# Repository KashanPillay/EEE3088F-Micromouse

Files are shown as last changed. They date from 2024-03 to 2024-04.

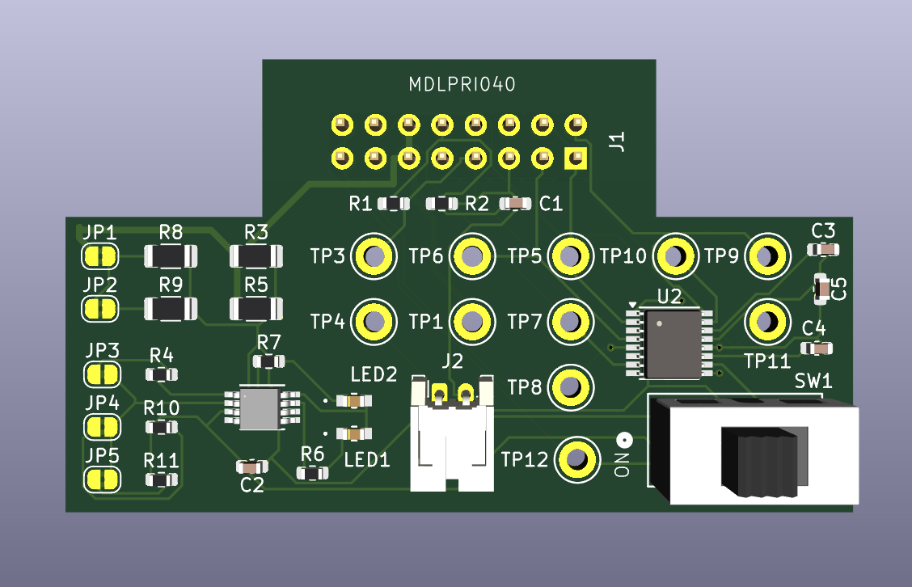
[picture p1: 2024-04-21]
Power Subsystem/Interim Report Figures/3D.png

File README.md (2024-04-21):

# EEE3088F-Micromouse
A repository to manage and control versions pertaining to the EEE3088F Micro-mouse Project and all sub-projects.
This GitHub contains 2 folders, each carrying relevant information regarding a specific subsystem: the first is Sensing and the second is Power. There are multiple folders within each subsystem folder. There is one containing all the datasheets for components selected for the final designs. These folders are labeled "Data sheets". In addition, there is a folder titled 'Interim Design Report' in each subsystem which contains the completed Interim Design Report. Lastly, all Gerber files and Bill Of Materials files can be found in the last folder. Thank you for visiting the GitHub :)

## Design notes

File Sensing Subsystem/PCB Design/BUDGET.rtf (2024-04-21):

BUDGET:

Sensor: SFH309 - $0.325/unit - $0.975
Emitter: TSAL6200 - $0.089/unit - $0.534

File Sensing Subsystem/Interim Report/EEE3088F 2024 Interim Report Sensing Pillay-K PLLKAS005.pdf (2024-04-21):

# Interim Design Report

Micromouse: Sensing Subsystem


Prepared by:
Kashan Pillay
PLLKAS005

Prepared for:
EEE3088F
Department of Electrical Engineering University of Cape Town

April 21, 2024

# Declaration

1. I know that plagiarism is wrong. Plagiarism is to use another’s work and pretend that it is one’s own.
2. I have used the IEEE convention for citation and referencing. Each contribution to, and quotation in, this report from the work(s) of other people has been attributed, and has been cited and referenced.
3. This report is my own work.
4. I have not allowed, and will not allow, anyone to copy my work with the intention of passing it off as their own work or part thereof.

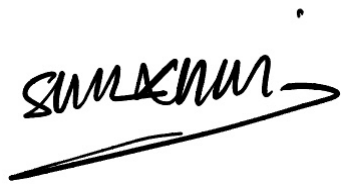
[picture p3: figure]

April 21, 2024

Kashan Pillay | Date

ii

# Contents

1 Introduction | 1
2 Requirements Analysis | 2
3 Subsystem Design | 5
4 Acceptance Testing | 10

iii

# Chapter 1

# Introduction

### 1.1 Problem Description

This project is a task in which a sensing subsystem is to be designed and manufactured for fitment in a fully functioning micro-mouse.
The greater project is a micro-mouse. A micro-mouse is in essence, a maze-solving robot. The focus of this project is on the hardware backing the robot. There are four aspects of the hardware to be taken into account when designing the specific subsystem solution - in this case the sensing subsystem -; the processor, the motherboard, sensing and power. The motherboard will be responsible for connecting all four PCBs and is the base that all other modules will connect to. The processor board - which makes use of an STM32L476 - will be the control module of the robot which will involve a small software aspect in order to see its functioning correctly. The power module powers all aspects of the robot and lastly, the sensing subsystem - around which this project report will be based - is responsible for the detection of the surroundings of the robot.
In keeping with the goal of the project, this specific subsystem (sensing) is to detect the presence of an obstacle (in the most likely case, a maze wall) in front of and to either side of the functioning micro-mouse. In addition, this subsystem should have the means to save power when not in operation while abiding by all the set-out requirements and specifications within the scope of work.

### 1.2 Scope and Limitations

The scope of this project is to design and manufacture a sensing subsystem that will provide information to the processor on whether there is an obstruction in the way of the micro-mouse. The processor and motherboard will be provided and the group partner is designing the power subsystem. Of the objectives of this subsystem, detection sits are the forefront. Detection needs to be in front of and on either side of the robot. In addition, the following objectives are also to be implemented:
- Designing for reliability.
- Taking into account power draw in order to ensure that the micro-mouse is able to solve the maze without the battery being drained completely.
- A small software aspect in order to properly integrate this subsystem with the micro-controller and visibly indicate its functionality.
There are several limitations that need to be considered:
- Design Limitation: The subsystem PCB should be a suitable size for the robot and compatible with the motherboard pin headers.
- Time Limitation: The final complete and working PCB is to be demonstrated on 13/05/2024.
- Cost Limitation: There is a cost restriction of $16.50 for both boards ($8.25 per board).

### 1.3 GitHub Link

Group 62 GitHub link. (https://github.com/KashanPillay/EEE3088F-Micromouse)

# Chapter 2

# Requirements Analysis

### 2.1 Requirements

The requirements for a micro-mouse sensing module are described in Table 2.1 below.

Requirement ID | Description
UR01 | The design must maneuver within the confines of the maze.
FR01 | The design PCB should be an appropriate size.
FR02 | The design PCB must cost within the specified budget.
UR03 | The design must detect obstacles
FR03 | The design must be able to indicate location/detection ability.
UR04 | The design must provide real-time input to the micro-controller.
FR04 | The design PCB must be compatible with the motherboard.
UR05 | The design must be powered externally.
FR05 | The design must adhere to power and current restrictions.
UR06 | The design must have a power-saving functionality.
FR06 | The design input supply must be pulse width modulated.
UR07 | The design components must all be sourced from the manufacturer.
FR07 | The design must be manufactured by a specific company and all components must be specified.

Table 2.1: User[UR] and Functional[FR] requirements of the sensing subsystem design.

### 2.2 Specifications

The specifications, refined from the requirements in Table 2.1, for the micro-mouse sensing module are described in Table 2.2.

Specification ID | Description
SP01 | The PCB design must not exceed the bounds of an 85mm² square.
SP02 | The design must not exceed $8.25 per board ($16.50 total).
SP03 | The design must use a different LED to indicate detection - in the front, left or right - of the three available LEDs.
SP04 | The design PCB must be compatible with a 2x14 (2.4mm pin pitch) pin header.
SP05-1 | The design must be powered by 3.5V to 3.7V.
SP05-2 | The design must have a current draw of no more than 400mA.
SP06 | The pulse width modulation must be set to 50%.
SP07 | The manufacturing must be with JLCPCB and all components must be specified on the production files with a stock of more than 1000.

Table 2.2: Specifications[SP] of the sensing subsystem derived from the requirements in Table 2.1.

### 2.3 Testing Procedures

A summary of the acceptance testing [AT] procedures detailed in chapter 4 is given below in Table 2.3. Reference Key:
’AT’ - Acceptance Testing; ’UT’ - Unit Testing; ’UAT’ - User Acceptance Testing; ’BAT’ - Business

2.4. Traceability Analysis

Acceptance Testing.

AT ID | AT Type | Description
AT01 | UAT | Measure the manufactured PCB or ensure the dimensions of the PCB enclosed in the production files are adequate.
AT02 | BAT | Review the manufacturing order cost.
AT03-1 | UT | Observe a different LED turn on for detection in front of and on either side of the robot and no LED turning on when no detection.
AT03-2 | UT | Measuring the voltage across the emitters of the sensing circuit.
AT03-3 | UT | Measuring the output voltage of the sensing circuit.
AT04 | UT | Using a calliper to measure pin header through-hole connections.
AT05-1 | UT | Measuring the input voltage of the sensing circuit.
AT05-2 | UT | Measuring the input current of the sensing circuit.
AT06 | UT | Ensuring the micro-controller has been set to provide an output signal that has a duty cycle of 50%.
AT07 | BAT | Review the manufacturing bill of materials.

Table 2.3: Acceptance Testing [AT] descriptions derived from the table of requirements in Table 2.1.

### 2.4 Traceability Analysis

The show how the requirements, specifications and testing procedures all link, Table 2.4 is provided.

| Requirements | Specifications | Acceptance Test
1 | UR01,FR01 | SP01 | AT01
2 | FR02 | SP02 | AT02
3 | UR03, FR03 | SP03 | AT03-1, AT03-2, AT03-3
4 | UR04, FR04 | SP04 | AT04
5 | UR05, FR05 | SP05-1, SP05-2 | AT05-1, AT05-2
6 | UR06, FR06 | SP06 | AT06
7 | UR07, FR07 | SP07 | AT07

Table 2.4: Requirements Traceability Matrix

### 2.4.1 Traceability Analysis 1

UR01 and so FR01 - the appropriate size requirement in order to allow for the robot to have adequate mobility within the maze is from which SP01, the specification that dictates the size of the PCB should be no greater than the bounds of an 85mm x 85mm square, can be derived. In order to ’test’ that this requirement is satisfied - AT01 is suggested, which is to measure the manufactured PCB or ensure the dimensions on the production files are sufficient.

### 2.4.2 Traceability Analysis 2

From FR02, requiring the cost of the PCB manufacturing to be within a certain budget, SP02 -dictating that the design should not cost more than $8.25 per board ($16.50 total) - can be derived. These can be verified through AT02 which entails reviewing the manufacturing order cost to ensure that it is below the specified limit.

2.4. Traceability Analysis

### 2.4.3 Traceability Analysis 3

UR03 and so FR03 - the aspect that requires the system to detect obstacles and indicate its location gives rise to the specification SP03 which is that the design must use a different LED to indicate detection in the front, left and right of the robot. To test for this, we can use AT03-1, AT03-2 and AT03-3. AT03-1 indicates that to test for successful application of requirements, we should observe a different LED turn on for detection at each location and no LED being on when there is no detection. AT03-2 suggests measuring the voltage across the emitters in order to ensure that they are functioning as required and AT03-3 suggests measuring the voltage output of each of the three sensing circuits to observe that a high output is at the circuit of the location in which there is an obstacle.

### 2.4.4 Traceability Analysis 4

UR04 and FR04 - is the requirement that indicates that the design must provide a real time input to the micro-controller (UR04) and to do this the design PCB must be compatible with the motherboard pin headers (FR04) leads to SP04 which specifies that the design PCB must be compatible with a 2x14 (2.4mm pin pitch) pin header. In order to validate this requirement, AT04 suggests using a calliper to measure the pin header through hole connections present in the design.

### 2.4.5 Traceability Analysis 5

UR05 and FR05 - the requirements that dictate the power of the system should be external which requires observing power and current restrictions brings forth the specification which says that the design should be powered by 3.5V to 3.7V (SP05-1) while having a current draw of no more than 400mA (SP05-2). In order to validate this AT05-1 suggests measuring the input voltage of the sensing circuit to observe its adherence to the specification SP05-1 and AT05-2 suggests measuring the input current to observe its adherence to the specification SP05-2.

### 2.4.6 Traceability Analysis 6

UR06 indicates that the design input supply must have a power-saving functionality and that is accomplished by FR06 which entails having an input supply from a PWM port. This gives rise to specification SP06 which indicates that the pulse width modulation must be set to 50% and AT06 suggests a way to validate this is to observe the micro-controller port output has been set to the desired duty cycle.

### 2.4.7 Traceability Analysis 7

UR07 - the requirement that indicates that all components should be sourced from the PCB manufacturer can be accomplished by FR07 which states that the design must be manufactured by a specific company and all required components must be comprised within the BOM that will sent to them. From the above, we can see how SP07 came about which specifies that all manufacturing must be with JLCPCB with components being in stock in excess of 1000 units. AT07 suggests a way in which we can validate this which is to review the manufacturing bill of materials (BOM) in order to confirm that all required components were requested.

# Chapter 3

# Subsystem Design

### 3.1 Design Decisions

In this section, two of the most crucial aspects of the design process are going to be explored - Circuit Component Selection and PCB Design Selection. From these two aspects, various design decisions are going to be made.

### 3.1.1 Circuit Component Selection

- Infrared Sensor:
Three different infrared sensors were considered when designing this sensing subsystem the QRD1114, (https://www.onsemi.com/pdf/datasheet/qrd1114-d.pdf) SFH309FA (https://look.ams-osram.com/m/ce14b97f1982f0f/original/SFH-309-FA.pdf) and SFH205. (https://look.ams-osram.com/m/74e24481854c49f8/original/SFH-205-FA.pdf)
| QRD1114 | SFH309FA | SFH205
Pro | -Detection at up to 200mm. -Both an IR emitter and IR receiver. | -Sensitivity: 730-1120nm. -Size: 0.45mmx0.45mm. -Quantity in stock: 1632 -Cost: $0.2696 | -Sensitivity: 800-1100nm. -Size: 2.65mmx2.65mm. -Cost: $0.5940
Con | -Quantity in stock: 5. -Cost: $1.57 -Part Type: Extended | -Simply an IR receiver. -Part Type: Extended | -Quantity in stock: 0 - Simply an IR receiver. - Part Type: Extended

Table 3.1: Pros and Cons of the considered infrared sensors.

Selected Infrared Sensor Design Decision:
SFH309FA - based on the spectral sensitivity, small component size, large in stock quantity and low cost. This sensor is able to provide all the sensing abilities of the other two, with the added stock and cost benefits.
Discarded Infrared Sensor Design Decision:
QRD1114 - based on the low in stock quantity and high cost, this option was not feasible. SFH205 -due to the part not being in stock, it was immediately removed from consideration.
- Infrared Emitter:
Three different infrared emitters were considered when designing this sensing subsystem the QRD1114, (https://www.onsemi.com/pdf/datasheet/qrd1114-d.pdf) TSAL6100 (https://www.vishay.com/docs/81009/tsal6100.pdf) and TSAL6200. (https://www.vishay.com/docs/81010/tsal6200.pdf)
| TSAL6200 | TSAL6100 | QRD1114
Pro | -Peak emission: 940nm -Cost: $0.1194 -Quantity in Stock: 1476 | Peak emission: 940nm -Cost: $0.1205 -Half intensity angle: 10 deg | -Peak emission: 940nm. -Both an IR emitter and IR receiver.
Con | -Part Type: Extended -Half intensity angle: 17 deg | -Quantity in stock: 0 -Part Type: Extended | -Quantity in stock: 5. -Cost: $1.57 -Part Type: Extended

Table 3.2: Pros and Cons of the considered infrared emitters.

Selected Infrared Emitter Design Decision:
TSAL6200 - based off of the peak emission, large in stock quantity and low cost. This sensor is able to provide all the emitting abilities of the other two, with the added stock and cost benefits.
Discarded Infrared Emitter Design Decision:

3.1. Design Decisions

QRD1114 - based on the low in stock quantity and high cost, this option was not feasible. TSAL6100
- due to the part not being in stock, it was immediately removed from consideration - however was initially considered due to low cost and good angle of half intensity.
- Emitter Circuit Transistor:
Two bipolar junction transistors were considered for use as a switch in the emitter circuit of this sensing subsystem, the MMBT3904 and MMBT3904-G.
| MMBT3904 | MMBT3904-G
Pro | -Cost: $0.0097 -Quantity in stock: 1096136 -Part Type: Basic | -Cost: $0.0063 -Quantity in stock: 369248
Con | -Ic(max) is 200mA. -Power Dissipation: 200mW | -Part Type: Extended -Power Dissipation: 225mW

Table 3.3: Pros and Cons of the considered bipolar junction transistors.

Selected BJT Design Decision:
MMBT3904 - based off of the lower power dissipation, high in stock quantity and basic part classification. Discarded BJT Design Decision:
MMBT3904-G - based off of the greater power dissipation and extended part classification.
- E24 Component Values:
The use of E24 values was considered for the capacitors and resistors in this subsystem, however, since most resistors and capacitors are available in E12 values, basic components were easy to source in large quantities and low cost. In discarding the idea of E24 values, certain E12 values were selected to ensure that calculated component values were the same, if not extremely close. Some of the benefits of using the E24 series are the wider range of values as well as lesser associated tolerance.

### 3.1.2 PCB Design Selection

- Component Quantities/Configurations:
| Dual Emitter/Sensor Compo-nent | Single Sensor and Emitter | Single Sensor and Dual Emitter
Pro | -Single component allowing for PCB modularity. | -Cost: $0.38 per pair, so $1.167 per board. -Emission: sufficient IR light emission to be detected after re-flection. | -Cost: $0.50 per set, so $1.52 per board. -Emission: excellent IR light emission to be detected after re-flection.
Con | -Cost: $1.57 per unit, so $4.71 per board to allow for all direc-tion detection. -Emission: Combination compo-nent has a poor emittance and so additional emitters will be re-quired. | -Coverage: Detection of IR light from source in addition to re-flected light. -Reflection Loss:A single emitter results in a portion of IR light lost due to the angle at which the emitter and sensor are placed. | -Coverage: Detection of IR light from the source in addition to reflected light.

Table 3.4: Pros and Cons of the considered component quantities and configurations.

Selected Component Quantity Design Decision:
The single sensor and dual emitter design was selected due to the enhanced infrared emittance to ensure better detection for the required locations and distances. While the single sensor and emitter

3.1. Design Decisions

design was acceptable, the single sensor and dual emitter was within the confines of the budget and enhanced.
Discarded Component Quantity Design Decision:
The dual component design was discarded due to the cost implications and poor performance - relative to the other two designs. The single sensor and emitter was discarded for the enhanced ability of the dual emitter option.
- PCB Shape and Size:
| Square | Rectangle | T-shape
Pro | -Does not jut out of the robot allowing for good mobility. | -The large PCB coverage allows for sufficient room for all neces-sary circuitry. | -Sufficient room for all the nec-essary circuitry without protrud-ing from the robot allowing for range of motion.
Con | -Inadequate visibility (created by extension) to allow for com-plete obstacle detection on the left and right of the robot. | -Protruding from the robot, dis-abling a complete range of mo-tion within the confines of the maze. | -Minimal protruding which will reduce the motion of the robot in the maze.

Table 3.5: Pros and Cons of the considered PCB shape and size.

Selected PCB Shape and Size Design Decision: The chosen shape and size design decision is the T-shape. This is as a result of the minimal protruding, while still extending enough to allow for the IR sensor to adequately detect obstacles from a distance point of view as well allowing visibility
- in that the sensors visibility will not be hindered by parts of the robot.
Discarded PCB Shape and Size Design Decision: The square and rectangle designs were discarded. The square - due to the dimensions allowing for the sensors visibility to be hindered by parts of the robot and the rectangle due to its size disabling a wide range of motion for the robot within the walls of the maze (200x200mm).

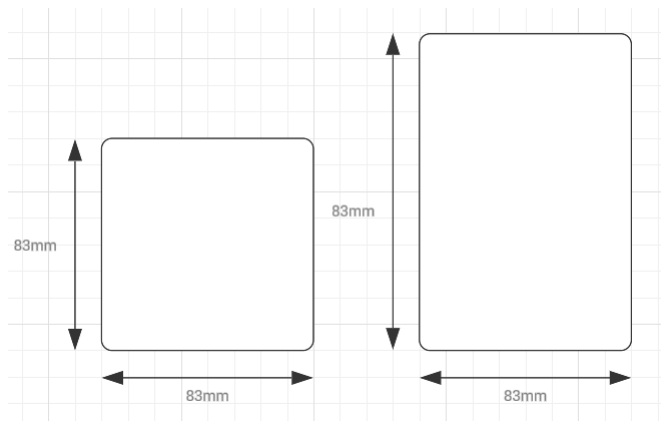
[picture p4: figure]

Figure 3.1: Square/Rect Shape

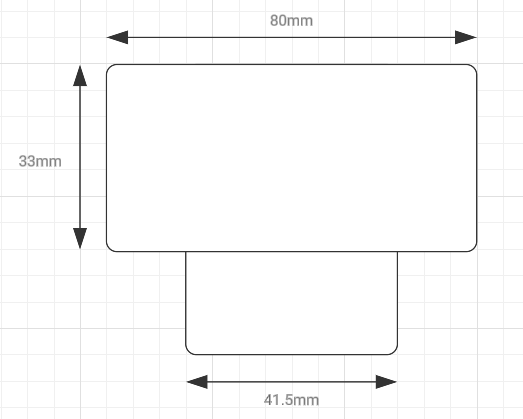
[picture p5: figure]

Figure 3.2: T Shape

- Sensor Placement and Angle:
Selected Sensor Placement and Angle Design Decision:
The chosen angle and placement was at 90 degrees with a wall to the left and right of the robot. This is in order to ensure maximum reflected IR light returning and not having to take into consideration IR reflected light lost due to the angle and distance at which the sensor is in relation to an obstacle on either side of the robot.
Discarded Sensor Placement and Angle Design Decision:
The 45 degree angle placement was discarded due to the poor detection ability of the sensors due to the distance at which the obstacle would be should the sensor be angled in this manner.

3.1. Design Decisions
| 45 degrees | 90 degrees
Pro | -Allows for better placed cir-cuitry on the manufactured PCB. | -Maximum detection ability due to proximity to reflective surface and orthogonal nature of reflec-tion.
Con | -Poor detection ability due to distance from the reflected sur-face/obstacle. | -PCB needs to be protruding in order to circumvent the sensors being obstructed by parts of the robot.

Table 3.6: Pros and Cons of the considered sensor placement and angle.

### 3.1.3 Final Design

The following design was selected based off of the above six unique design decisions. A sensing module is going to consist of a single SFH309FA infrared sensor accompanied by two TSAL6200 infrared emitters on either side. This is going to allow for adequate infrared light to be reflected and so detected by the SFH309FA. There are going to be three of these sensing modules that comprise the full sensing subsystem, one facing forward, one facing ninety degrees to the left and one facing ninety degrees to the right. So as to ensure the obstacle is within sensing range. These are all going to be mounted on a T-shaped PCB which allows for an adequate range of motion for the robot without compromising the visibility of the sensing module.

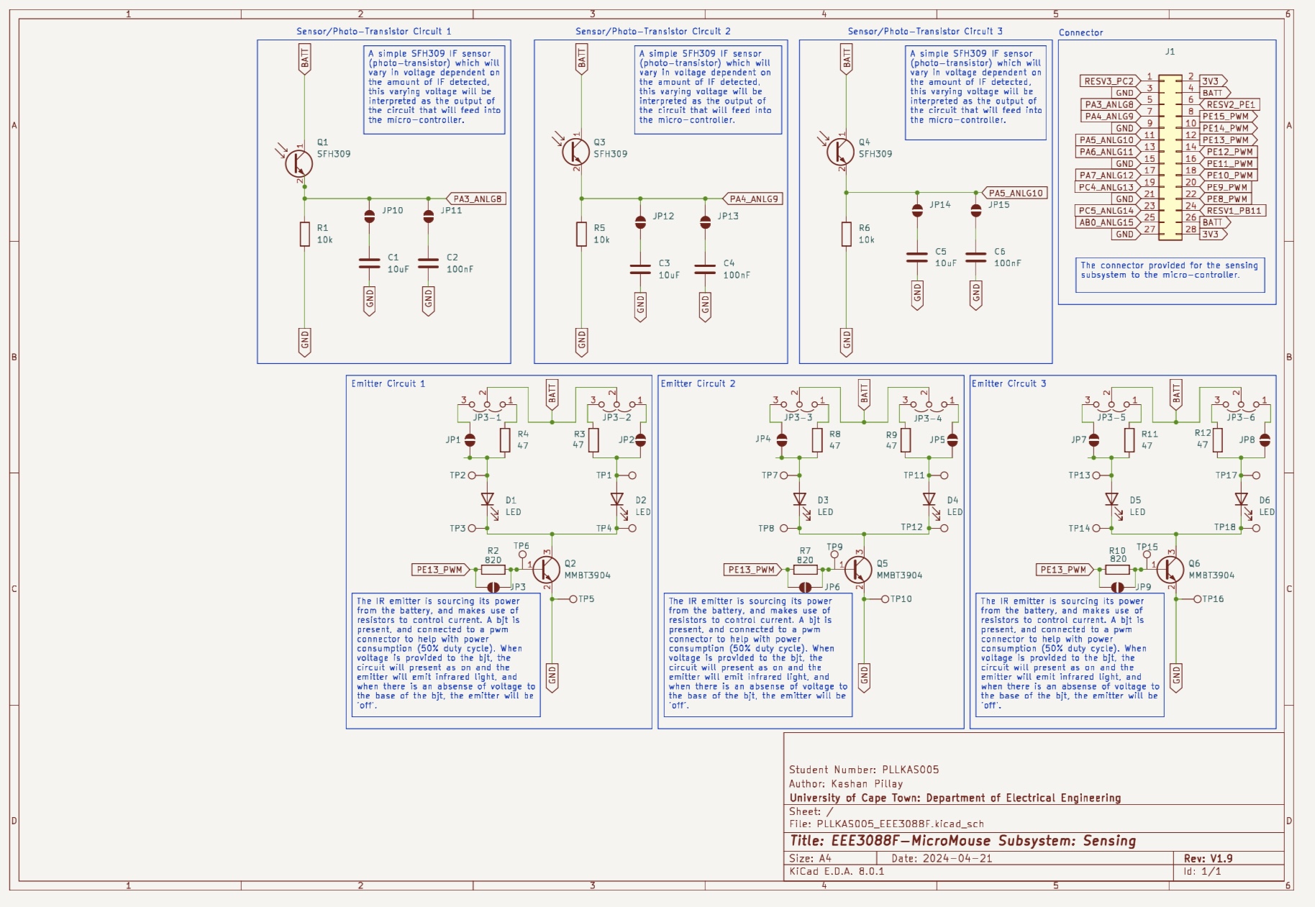
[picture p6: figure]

Figure 3.3: Final Design Schematic

CALCULATIONS: (Emitter Circuit 1)
Source Voltage = 3.3V, Current Draw = 0.1A, Forward Voltage = 1.2V ( TSAL6200) (https://www.vishay.com/docs/81010/tsal6200.pdf) R4=(3.3V-1.2V)/0.05A=42Ohms. E12: R4 = 47Ohms. Similarly R3=R8=R9=R11=R12= 47Ohms

PWM Voltage = 3.3V, Vce = 0.7V and Ib = 3.33mA (for Ic = 100mA) ( MMBT3904) (https://www.diodes.com/assets/Datasheets/MMBT3904.pdf) KVL:3v3-Vce=I(R2). R2=(3.3V-0.7V)/0.0033A=787Ohms. E12: R2=820Ohms. Similarly R7=R10=820Ohms.

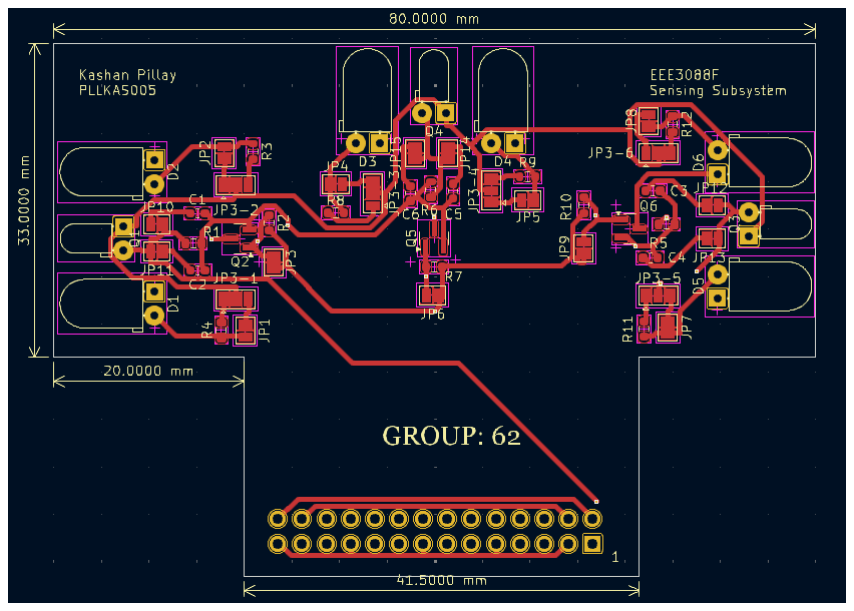
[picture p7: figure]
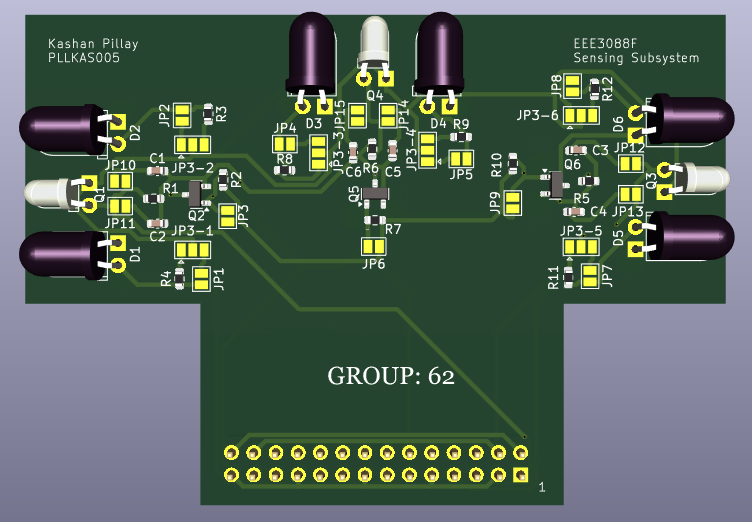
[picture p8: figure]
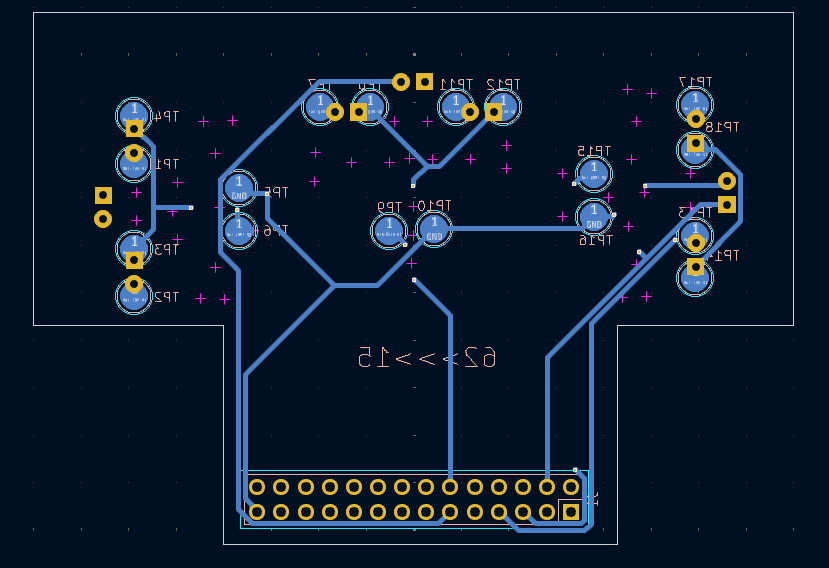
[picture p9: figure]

(a) Front PCB | (b) Back PCB | (c) 3D PCB

Figure 3.4: PCB

3.2. Failure Management

### 3.2 Failure Management

Below, Table 3.7 summarises the precautions taken to account for design errors/flaws.

Measure | Description
3-Point Jumpers (open) | i. These jumpers have been used at the voltage input of both branches of each emitter circuit. This jumper allows for the use of solder to connect the input voltage to a branch of choice in order to resolve a calculation error for the resistor at this point.
Test Points | i. These have been used to provide the voltage drop across the infrared emitter in order to ascertain the functional status of this component. ii. These have been used to provide the voltage drop across the base-emitter junction of the bipolar junction transistor (emitter circuit) in order to ensure that the transistor is operating in the desired (linear) region.
Pad-Jumper (open) | i. These have been used in the additional branch of the input voltage to each emitter circuit. This allows the addition of a different valued resistor or to completely short the branch. ii. These have been used across the resistor in the base of the bjt in order to all for the decrease of resistance by the addition of a resistor in parallel. iii. These have been used as connectors to two different capacitors at the output of each infrared sensor circuit in order to allow for selection between the two different valued components.
Additional Ca-pacitors | i. These are connected to the circuit using open solder pad jumpers in order to allow for error catching in the integration with the ADC.

Table 3.7: Failure Management Measures

### 3.3 System Integration and Interfacing

Below, Table 3.8 and Figure 3.5 summarise the integral integration and interfacing aspects.

Interface | Description | Pins/Output
I001 | Sensing-subsystem to Processor-subsystem (housing the STM32L476) in order for the micro-controller (ADC) to receive the output of the sensor circuit (obstacle detection) of the sensing subsystem. | • ANLG8: PIN5 to STM PA3 • ANLG9: PIN7 to STM PA4 • ANLG10: PIN11 to STM PA5
I002 | Processor-subsystem (housing the STM32L476) to Sensing-subsystem in order for there to be power from the source to the emitter circuit of the sensing subsystem. | • STM BATT to PIN26
I003 | Sensing-subsystem to Processor-subsystem (housing the STM32L476) in order to have ground as a reference. | • PIN21 to STM GND
I004 | Processor-subsystem (housing the STM32L476) to the Sensing-subsystem in order to reduce power consumption a PWM signal is supplied to the base of the emitter circuit, control the bjt which is acting as a switch. | • PWM: STM PE13 to PIN12

Table 3.8: System Interfacing Table

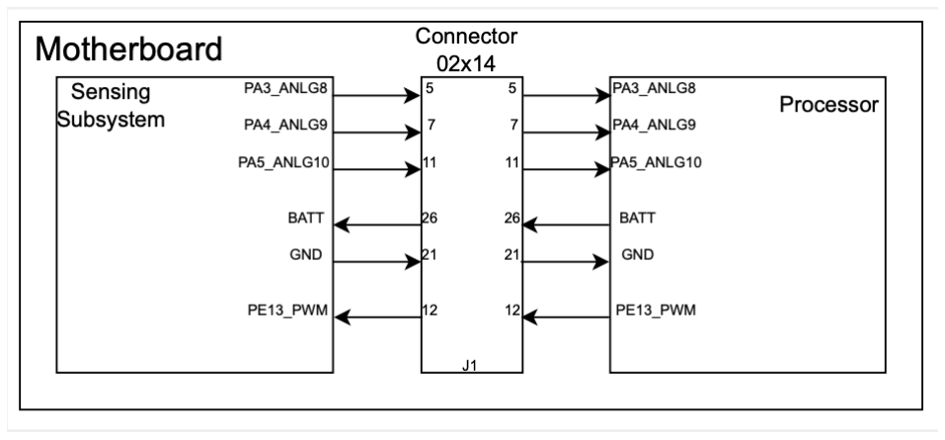
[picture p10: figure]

Figure 3.5: System Interfacing Diagram

# Chapter 4

# Acceptance Testing

### 4.1 Tests

AT ID | Description | Testing Procedure | Pass Criteria
AT01 | (User Acceptance Testing) Measure the man-ufactured PCB or ensure the dimensions of the PCB enclosed in the production files are adequate. | i. Measure the length of the manufactured PCB with a PCB ruler. ii. Measure the breadth of the manu-factured PCB with a PCB ruler. | i. Dimension of length less than 85mm. ii. Dimension of breadth less than 85mm.
AT02 | (Business Acceptance Testing) Review the manufacturing order cost. | i. By looking at the confirmation of receipt or order receipt the cost can be confirmed. | i. The total cost being less than $16.50.
AT03-1 | (Unit Testing) Observe a different LED turn on for detection in the front of and on either side of the robot and no LED turning on when no detection. | i. Place an obstacle in front of the powered micro-mouse ii. Place an obstacle to the left of the micro-mouse. iii. Place an obsta-cle to the right of the micro-mouse. iiii. Have no obstacles in the surroundings of the robot. | i. LED one lights up. ii. LED two lights up. iii. LED three lights up. iiii. None of the three LEDs turn on.
AT03-2 | (Unit Testing) Measuring the voltage across the emitters of the sensing circuit. | i. Using a voltmeter, measure the voltage across the emitters us-ing the placed testing points. | i. Voltage in the range of 1.2-1.6V.
AT03-3 | (Unit Testing) Measuring the output voltage of the sensing circuit. | i.Using a voltmeter, measure the output voltage across the placed test points. | i. The voltage being in the range of 0.5-3.3V. (there should be an out-put voltage - due to ambient light)
AT04 | (Unit Testing) Measuring the pin header through-hole connections. | i. Using a caliper, mea-sure the through-hole connections. | i. The measurement being in the range of 2.4mm.

4.1. Tests
AT ID | Description | Testing Procedure | Pass Criteria
AT05-1 | (Unit Testing) Measuring the input voltage of the sensing circuit. | i.Using a voltmeter, measure the input volt-age with respect to ground. | i. The input voltage should be in the range of 3.3V.
AT05-2 | (Unit Testing) Measuring the input current of the sensing circuit. | i.Using an ammeter, measure the input cur-rent of the circuit. | i. The current should be less than 100mA.
AT06 | (Unit Testing) Ensuring the micro-controller has been set to provide an output signal that has a duty cycle of 50%. | i. Using the suggested interface software, en-code the required duty cycle. | i.The duty cycle should be less than 100% to ensure any sort of power saving.
AT07 | (Business Acceptance Testing) Review the manufacturing bill of materials. | i.By looking at the con-firmation of receipt or order receipt the com-ponent selection can be confirmed. | i. Components should be populated on PCB and the order con-firmed.

Table 4.1: Subsystem Acceptance Tests

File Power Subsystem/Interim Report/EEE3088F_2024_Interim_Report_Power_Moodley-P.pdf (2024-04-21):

# Interim Design Report

Micromouse Power Subsystem


Prepared by:
Priya Moodley
MDLPRI040

Prepared for:
EEE3088F
Department of Electrical Engineering University of Cape Town

April 21, 2024

# Declaration

1. I know that plagiarism is wrong. Plagiarism is to use another’s work and pretend that it is one’s own.
2. I have used the IEEE convention for citation and referencing. Each contribution to, and quotation in, this report from the work(s) of other people has been attributed, and has been cited and referenced.
3. This report is my own work.
4. I have not allowed, and will not allow, anyone to copy my work with the intention of passing it off as their own work or part thereof.

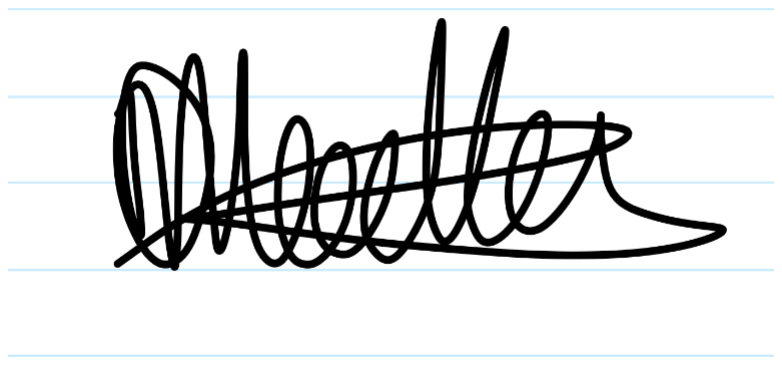
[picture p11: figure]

April 21, 2024

Name Surname | Date

# Contents

1 Introduction | 1
2 Requirements Analysis | 2
3 Subsystem Design | 5
4 Acceptance Testing | 10

# Chapter 1

# Introduction

### 1.1 Problem Description

The project’s problem is to design and manufacture a power subsystem that is capable of powering an entire micro-mouse system.

The greater project comprises four subsystems that interface with one another, each of which has a related board. The motherboard carries two motors and is the foundation for the other boards: the processor board, sensor board, and power board (upon which the power subsystem will be implemented). The processor board contains the microcontroller and its related input/output pins which allow for operations to be dictated as required. The sensor subsystem can determine whether there is an obstruction in front and on either side of the robot and output that to the user as well as change its direction according to its findings. The power subsystem is responsible for powering each of the above-mentioned boards which, if they behave as intended, allow the robot to solve a maze correctly.

### 1.2 Scope and Limitations

The power subsystem will provide power to the two motors, the STM32L476 microcontroller on the processor board, and the sensors contained within the sensing subsystem. This ensures that all subsystems receive the required power to function as intended, and should it not behave correctly, the micro-mouse operation will be affected. Additionally, the power board will be fully equipped with a charging circuit to charge the battery. Without a functional charging circuit, the power provided to the above-mentioned subsystems will be limited to a single battery life. The power board containing the power subsystem will be an appropriate size as the micro-mouse in itself will be physically small and a large power board will affect the micro-mouse’s center of mass and restrict the motion of the mouse in a maze.

There will be an ON/OFF switch with specific current limitations. Furthermore, there are specific connectors that must be catered for to allow for interfacing with the other subsystems. There is a financial limitation placed on the subsystem as the component cost budget for a single board is $ 8.25, which includes the fee for extended components. In addition, the time limitation states that the design must be completed by 24 March 2024 to allow for the manufacturing process to begin and the completed power board must be prepared for presentation on 8 May 2024.

### 1.3 GitHub Link

Click here to visit Group 62’s GitHub (https://github.com/KashanPillay/EEE3088F-Micromouse)

# Chapter 2

# Requirements Analysis

### 2.1 Requirements

The requirements for a micromouse power module are described in Table 2.1.

Table 2.1: User and functional requirements of the power subsystem.

Requirement ID | Description
UR01 | Provide power to the motors.
FR01 | A motor driver circuit is used to provide the appropriate voltages to the motors.
UR02 | Provide power to the microcontroller.
FR02 | Have a connection from the microcontroller’s battery pin to the battery.
UR03 | Design must only include components from a PCB manufacturing company.
FR03 | All components must be found on JCLPCB.
UR04 | Fit onto the motherboard.
FR04 | Must have a tab with the connectors on the power board.
UR05 | Must be able to move within a maze.
FR05 | Ensure the board’s length does not interfere with the micromouse’s center of rotation.
UR06 | Adhere to a strict budget.
FR06 | Select components whose sum does not exceed the budget.
UR07 | Design must be able to be switched ON and OFF.
FR07 | Have a physical ON/OFF switch that controls voltage to the other components.
UR08 | Monitor the battery’s state of charge.
FR08 | Provide an analog connection with the voltage of the battery to the microcontroller.
UR09 | Charge the battery.
FR09 | Have a battery charging circuit that accounts for when the external voltage source is plugged in and when it is removed.

### 2.2 Specifications

The specifications, refined from the requirements in Table 2.1, for the micromouse power module, are described in Table 2.2.

Table 2.2: Specifications of the power subsystem derived from the requirements in Table 2.1.

Specification ID | Description
SP01 | Motors have a maximum current draw of 200mA at 4.2V from the battery.
SP02 | 2x8 JST (2.54mm pin pitch) Pin Header joins the battery and microcontroller pins.
SP03 | There must be a stock of over 500 on JCLPCB for each component.
SP04 | The centered tab has a minimum height of 18mm and a maximum width of 35mm.
SP05 | The board length must not exceed 100mm.
SP06 | The components must cost under $ 8.25 per board, including extended part fees.
SP07 | Use a switch to turn the power board ON/OFF and ensure it is labeled on the board.
SP08 | Monitors and sends the battery’s state of charge to the BATT-ADC pin.
SP09 | Attach the battery to the power board using a two-pin 2mm JST pin header.
SP10 | The max discharge must be at 0.5C for the 3.7V 800mAh Lithium-Polymer battery.

2.3. Testing Procedures

### 2.3 Testing Procedures

A summary of the testing procedures detailed in chapter 4 is given in Table 2.3.

Table 2.3: A brief review of the testing procedures

Acceptance Test ID | Description
AT01 | Check that motors receive power.
AT02 | Check that the microcontroller is receiving power.
AT03 | Check that all components are within acceptable stock limits on the JLCPCB website.
AT04 | Measure the width and length of the tab.
AT05 | Measure the width and length of the entire power board.
AT06 | Calculate the total component cost and verify it on the JLCPCB website.
AT07 | Check that the switch behaves correctly.
AT08 | Code the microcontroller to display the state of charge from the ADC pin.
AT09 | Check that the battery charging circuit is operational.

### 2.4 Traceability Analysis

The show how the requirements, specifications, and testing procedures all link, Table 2.4 is provided.

Table 2.4: Requirements Traceability Matrix

# | Requirements | Specifications | Acceptance Test

1 | UR01, FR01 | SP01 | AT01
2 | UR02, FR02 | SP02 | AT02
3 | UR03, FR03 | SP03 | AT03
4 | UR04, FR04 | SPO4 | AT04
5 | UR05, FR05 | SP05 | AT05
6 | UR06, FR06 | SP06 | AT06
7 | UR07, FR07 | SP07 | AT07
8 | UR08, FR08 | SP08 | AT08
9 | UR09, FR09 | SP09, SP10 | AT09

### 2.4.1 Traceability Analysis 1

UR01 states that the motors must receive power from the power subsystem. In FR01 it is explained that a motor driver circuit must be used to do so, and SP01 states the maximum current through the output of that circuit. To test this AT01 is suggested because it verifies that power is being sent to the motors and that they are within the accepted current limits.

### 2.4.2 Traceability Analysis 2

From UR02, which says that the microcontroller is powered by the power subsystem, and FR02 which expands that a connection is required, SP02 can be derived because a specific pin header is needed to correctly interface with the other subsystems. AT02 ensures that the power is being correctly provided to the microcontroller.

2.4. Traceability Analysis

### 2.4.3 Traceability Analysis 3

From UR03 and FR03, which state the requirement that all components must come from the same PCB manufacturing company- JLCPCB - SP03 can be derived as there needs to be adequate availability for a component to be populated on a board. These can be tested through AT03 which checks the quantity in stock for each component on the JLCPCB website.

### 2.4.4 Traceability Analysis 4

As seen in UR04 and FR03, the power board must have a tab with the specific dimensions titled in SP04 to ensure that it fits onto the motherboard comfortably. AT04 checks that these conditions are satisfied by measuring the dimensions and comparing them against the required values.

### 2.4.5 Traceability Analysis 5

UR05 and FR05 are concerned with the size of the power board as it will affect the movement of the micromouse as a whole, SP05 is a specification derived from the overall measurements of the micromouse and ensures that the power board does not extend too far past the end of the micromouse. This is tested through AT05 which measures the length of the power board.

### 2.4.6 Traceability Analysis 6

From UR06 and FR06, there is a strict financial requirement where the component cost cannot exceed $ 8.25 per board as specified in SP06, and AT06 verifies that the financial requirements are adhered.

### 2.4.7 Traceability Analysis 7

UR07 and FR07 state the need for a physical ON/OFF switch and SP07 details the necessary condition for a label on the board to ensure there is proper communication from the board to those using it. AT07 uses a continuity test on a multimeter to ensure that it is working as intended.

### 2.4.8 Traceability Analysis 8

UR08 and FR08 ensure that the battery’s state of charge is monitored and sent to a specific pin in the microcontroller, specified in SP08 and verified by AT08 which uses the microcontroller to display the output of the BATT-ADC pin.

### 2.4.9 Traceability Analysis 9

The battery charging circuit, explained by UR09 AND FR09 with specifications from SP09 and SP10 outlines the need for a functional battery charging circuit that is effective when the battery is plugged into a voltage source and once it is removed. The output of the circuit is tested by AT09.

# Chapter 3

# Subsystem Design

### 3.1 Design Decisions

### 3.1.1 Component Selection

Motor Driver Circuit

For the motor driver circuit, multiple options were considered. An H-Bridge configuration is the most common solution as it allows for bidirectional control of the motor and speed control from Pulse-Width Modulation (PWM) signals from the microcontroller. Some H-Bridges can be constructed from scratch with MOSFETs or switches, and there are Integrated Circuits (ICs) that contain those components as internal circuitry. Ultimately, as the budget permitted it, an IC was chosen. This was a more promising route as there was less room for error than if the circuit was designed from scratch. In addition, a Dual H-Bridge IC will contain the functionality for both motors in a single component which saves space on the board and expenses if a suitable one is picked.

JLCPCB contains a multitude of Dual H-Bridge Motor Driver ICs, however, parts were filtered based on the following criteria:
- There must be stock
- The part cannot be unavailable
- There must be an English data sheet or an English version available online
- The supply voltage or PWM signal voltage must be in the range provided (3.7V and 3.3V, respectively)
- The IC must be able to handle a maximum of 400mA on the motor side
- It must be a dual H-Bridge Motor, therefore able to operate two DC motors as a single device • The IC must only require inputs from I/O Pins that are available to the power board

The first 3 viable options that fit all criteria are shown below in Figure 3.1:

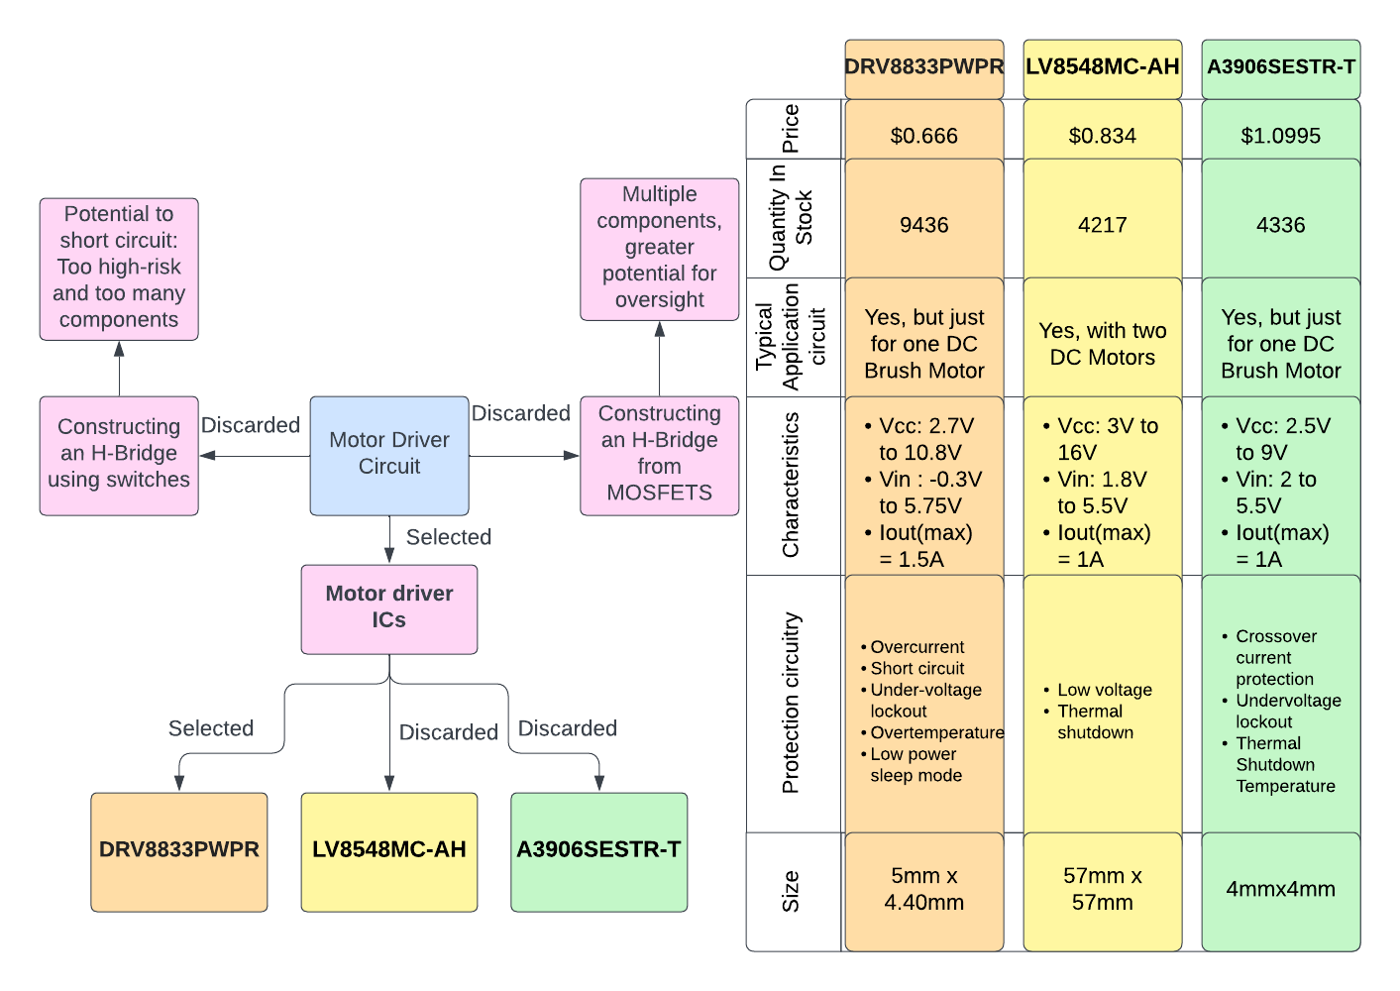
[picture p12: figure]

Figure 3.1: Flow Chart with Motor Circuit options and Table comparing Motor Driver ICs

3.1. Design Decisions

As seen in the figure above, the DRV8833PWPR is the cheapest option, has more protection circuitry, and is physically small so as not to take up too much space on the power board, it fulfills all the voltage and current requirements. Thus, the DRV8833PWPR whose data sheet can be found here (https://wmsc.lcsc.com/wmsc/upload/file/pdf/v2/lcsc/1810151712_Texas-Instruments-DRV8833PWPR_C50506.pdf) was the final choice for the Motor Driver IC.

Battery Charging Circuit

For the battery to be charged, the appropriate circuit must be constructed. After a search on JLCPCB, it was found that there are three basic Battery Charging ICs that have the same functionality as building a battery charging circuit. The English data sheet for the TP4057 could not be found, so the selection was between the TP4054 and the TP4056. Both components are preset to 4.2V Charge Voltage and are adaptable to charging Single Cell Li-Ion Batteries directly from the USB Port. These are very similar components but their differences are recorded in the table below:

Table 3.1: Table comparing two Battery Charging ICs

| TP4054 | TP4056
Price | $0.1289 | $0.1724
Quantity in Stock | 9468 | 107298
BAT Pin Current(max) | 800mA | 1200mA

Ultimately, the choice was made as the TP4056 contained an informative table on exactly which resistors to pick for specific desired battery currents while the TP4054 has many varying equations which resulted in various contradictory answers for the resistance. The price difference (among others) is minimal between the two ICs. The data sheet for the TP4056 can be found here. (https://dlnmh9ip6v2uc.cloudfront.net/datasheets/Prototyping/TP4056.pdf)

Switch

There are only extended part switches that were considered for this project. A slide switch was considered the most appropriate as it has a definitive state of ’ON’ and ’OFF’. After filtering out those that were not in stock, four hundred and twenty-five options were remaining.

Since the switch functionality is fairly simple, the first compatible switch on the list with the right specifications was selected. That was the SS-12D10G5 slide switch. The cost is $0.2618 and the average cost for slide switches varies from around $0.1 to $0.4 so this was an acceptable figure and there are 2362 in stock. Additionally, it is an adequate size to allow for easy switching but not too bulky for the final power board. The data sheet can be found here. (https://wmsc.lcsc.com/wmsc/upload/file/pdf/v2/lcsc/2110100830_XKB-Connectivity-SS-12D10G5_C2884744.pdf)

### 3.1.2 Calculations and Value Selection

To report the state of charge of the battery, a voltage divider consisting of two resistors and a capacitor is used. The value of the capacitance is 10uF to fit in with the E12 Series component values and its presence is needed to compensate for load capacitance. Since the microcontroller cannot handle an input of the full battery voltage (4.2V), the voltage divider scaled the voltage down by 50% as a precaution and, 2.1V is considered ’fully charged’. The values selected for the voltage divider are components that are part of the E12 Series and a simple combination that results in the desired scaling, as shown below.

3.2. Failure Management

Assume BattADC and BATT have volts as units:
BattADC = BATT * (R2/R1+R2) = BATT(1kOhm/2kOhm)= 1/2 BATT in Volts

The Motor Driver IC datasheet contained a typical application diagram, with exact capacitor values to ensure the motor driver circuit functions as intended. These values were verified as part of the E12 Series and included in the circuit as seen in the final schematic in the next subsection.

The resistors in the Battery Charging circuit were selected based on recommended values in the datasheet for the IC for charging a single-cell LI-Po battery.

### 3.1.3 Final Design

The following design contains all the selected components from the above subsection. This design was chosen as the switch needed to be in an accessible area for easy switching. The Test Points became quite cluttered when they were adjacent to their relative components but when aligned to one side the board appeared neater. The solder jumpers needed to be on the side of the board for easy access as it is simpler to solder onto the side instead of right in the middle of a board.

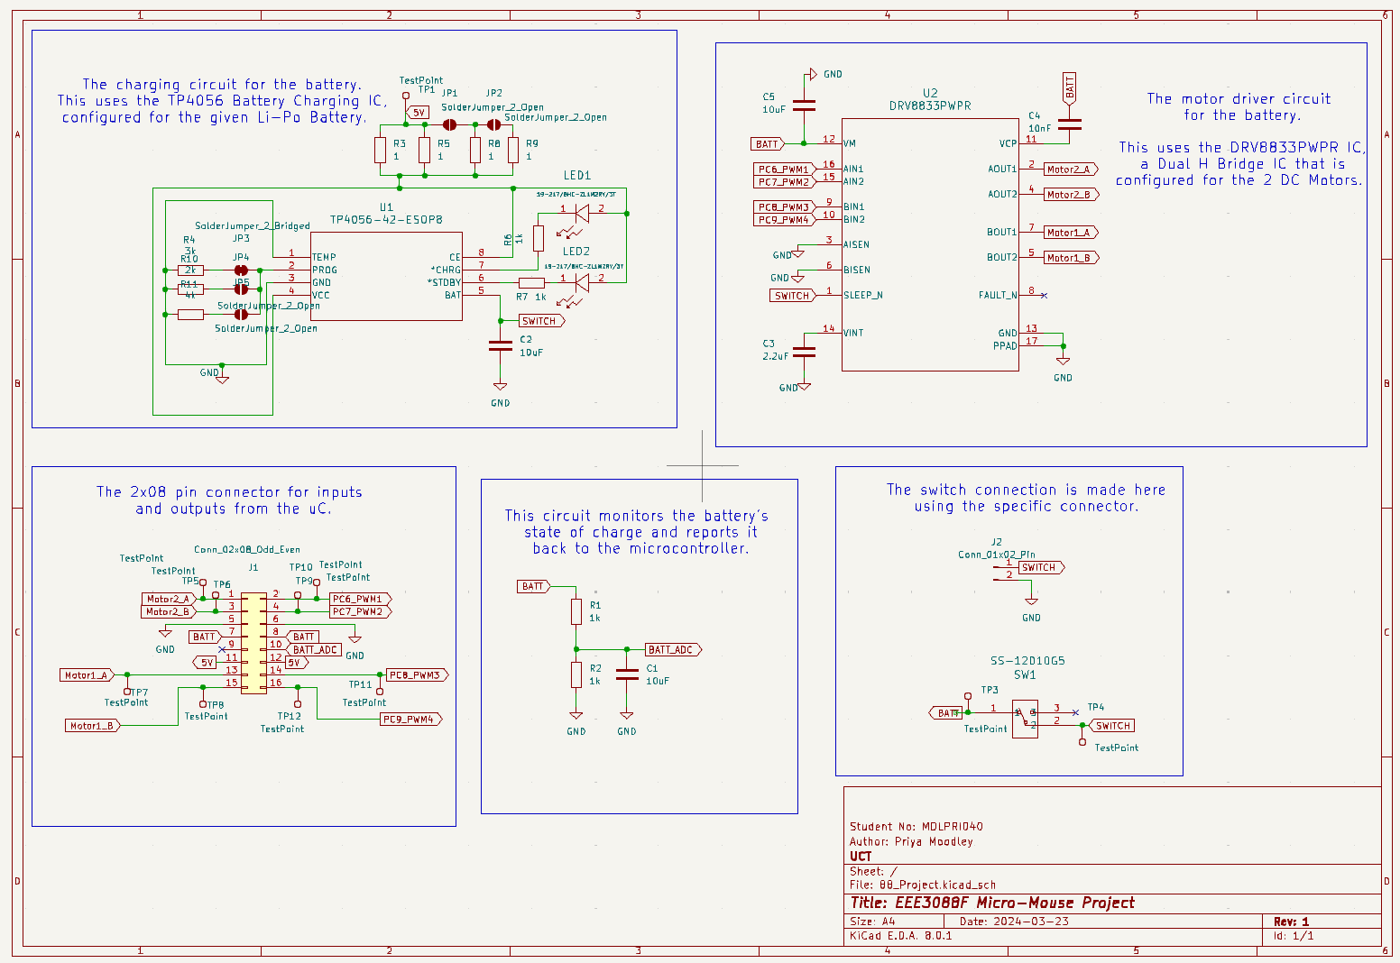
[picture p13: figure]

Figure 3.2: Schematic

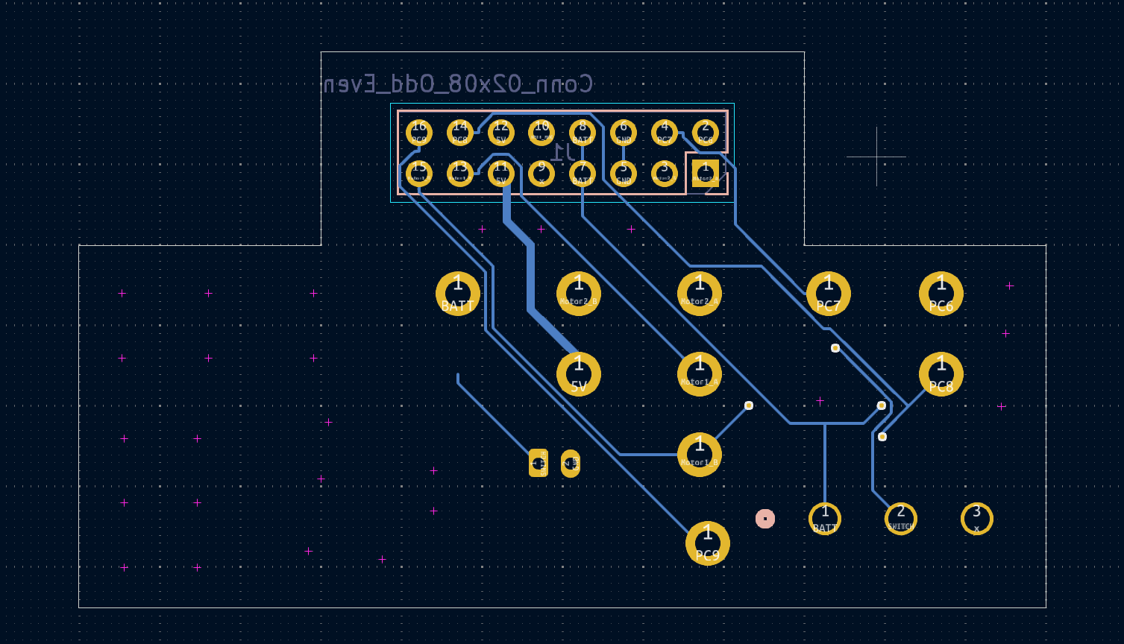
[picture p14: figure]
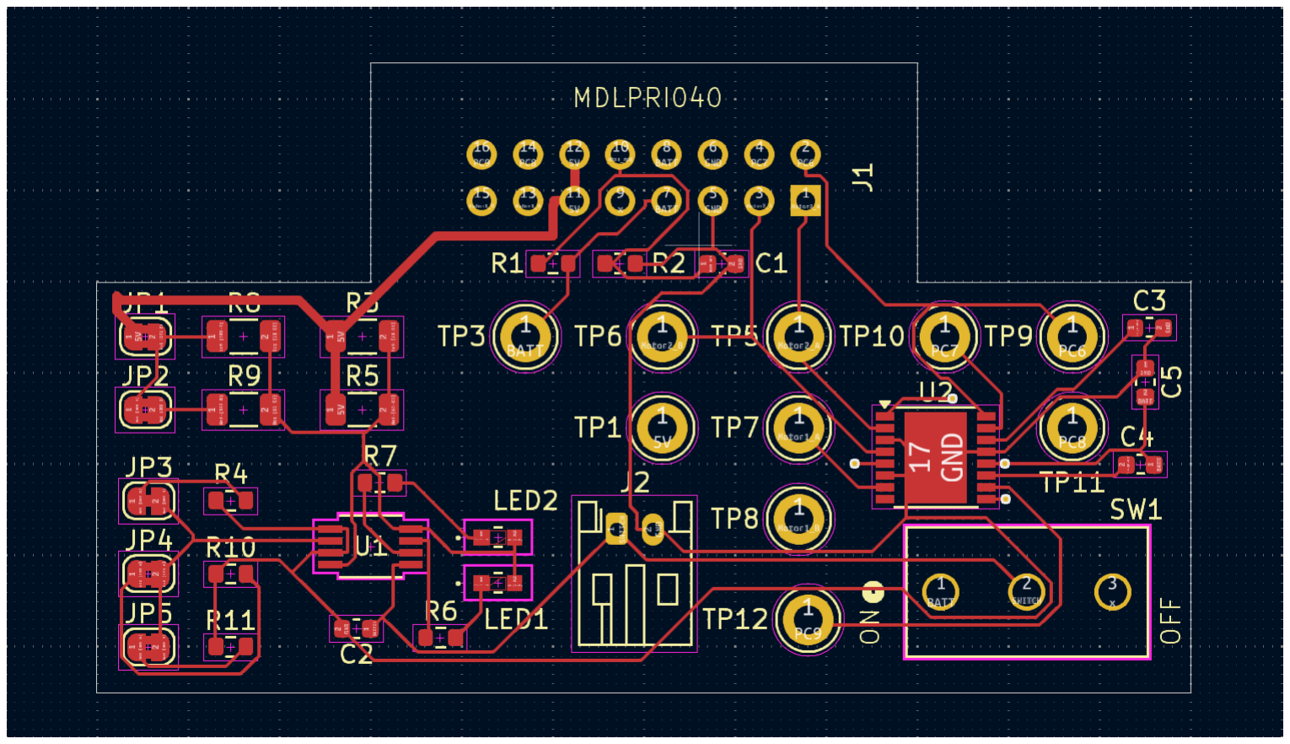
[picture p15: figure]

(a) Front of the PCB | (b) Back of the PCB | (c) 3D version of the PCB

Figure 3.3: PCB

### 3.2 Failure Management

Since most of the components are ICs and have internal circuitry that cannot be modified, the replacement of components is difficult. The failure management for these components is essentially reliant on the testing to ensure that the components work as desired and if they do not, then understand

3.3. System Integration and Interfacing

exactly where the component failed. The table below outlines two instances where the resistor values were external to the IC and what other options are available should the initial choice not work.

Table 3.2: Table showing failure management methods

Name | Description
Resistor value 1 for Charging circuit. | The recommended resistance for the first resistor in the charging circuit with the IC is 0.25 Ohms. Since this is not available on JLCPCB, multiple 1 Ohm resistors have been placed in parallel to ensure a small enough resistance is achieved. They are added using solder-jumpers and will only be used if the initial resistors fail to work.
Resistor Value 2 for Charging circuit. | The resistor that sets the value for the current for the charging circuit. This value was selected based on the information given in the data sheet, however, multiple options are available and in the case that this value is incorrect and does not allow for charging, another one will be used.

### 3.3 System Integration and Interfacing

To integrate the power subsystem with the rest of the system, the main component used is the Pin Connector. This acts as a bus for connections with the microcontroller on the processor board as well as the motors on the motherboard. These connections are outlined in Table 3.3 and Figure 3.4 below.

Table 3.3: Interfacing specifications between the Power Board and the other subsystems

Interface | Description | Pins Relations
I001 | Power Board Pin Connector to Mo-tors for control of each motor. | • Pin Connector: Pin 1 to Motor 2: A • Pin Connector: Pin 3 to Motor 2: B • Pin Connector: Pin 13 to Motor 1: A • Pin Connector: Pin 15 to Motor 1: B
I002 | STM32L476 to Power Board Pin Connector for PWM signals to con-trol motors. | • STM PC6(Pin 6: PWM1) to Pin Connector: Pin 2 • STM PC7(Pin 7:PWM2) to Pin Connector: Pin 4 • STM PC8(Pin 4: PWM3) to Pin Connector: Pin 14 • STM PC6(Pin 3: PWM4) to Pin Connector: Pin 16
I003 | STM32L476 to Power Board Pin Connector for access to the 5V volt-age supply to charge the battery | • STM 5V USB(Pin 10) to Pin Connector: Pin 12. • STM 5V USB(Pin 10) to Pin Connector: Pin 11
I004 | Power Board Pin Connector to STM32L476 to send the microcon-troller information on the battery’s state of charge. | • Pin Connector: Pin 10 to STM 3V3 ADC(Pin 48: Analogue)
I005 | Power Board Pin Connector to STM32L476 to power the microcon-troller. | • Pin Connector: Pin 7 to STM VBAT(Pin 2) • Pin Connector: Pin 8 to STM VBAT(Pin 2)

3.3. System Integration and Interfacing

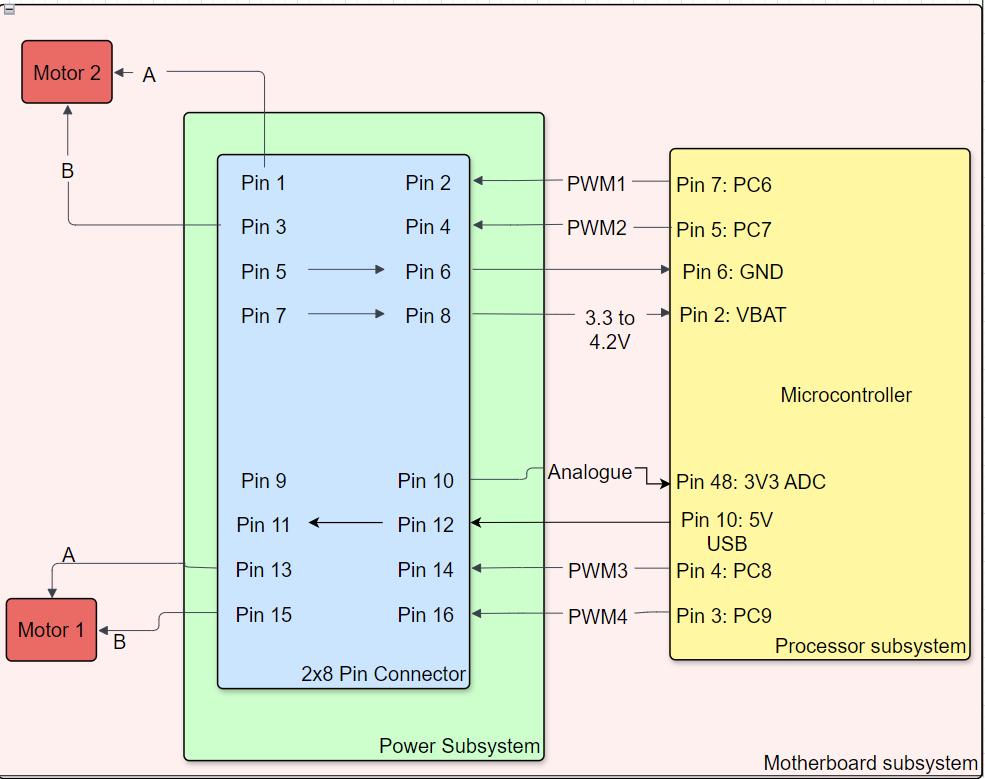
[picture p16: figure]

Figure 3.4: Interfacing Diagram of Power Subsystem with the other subsystems

# Chapter 4

# Acceptance Testing

### 4.1 Tests

Table 4.1: Power Subsystem acceptance tests

Test ID | Description | Testing Procedure | Pass/Fail Criteria
AT01 | Check that motors re- ceive power. | • Assume AT02 is passed and the microcontroller can send PWM sig- nals to the motors. • Assume AT07 is passed and the switch works as intended. • Ensure that the switch is ’ON’. • Set code on the microcontroller to send PWM signals to the specific pins connected to each motor. • Measure the voltage from Test Points 7 and 8 to GND to check the voltage going to Motor 1 A and B respectively is enough to switch on the motor. • Measure the voltage from Test Point 11 and Test Point 12 to GND to check the voltage going to Motor 2 A and B respectively is enough to switch on the motor

If the voltage measured at the test points goes high when the respective PWM signal is on that pin then the motor is driven correctly and the test is passed.

AT02 | Check that the mi-crocontroller receives power. | • Assume AT07 is passed. • Measure the voltage at TP3 as this is connected to the microcontroller pin. • Check if the voltage matches the battery voltage. | If the voltage matches, the bat-tery voltage is supplied to the microcontroller and the test is passed.
AT03 | Check the bill of materi-als. | • Look at the bill of materials file generated by KiCAD and ensure each component matches its value and can be found and used on JL-CPCB. | If all the desired components are there, the test is passed, else it is failed.
AT04 | Measure the width and length of the tab. | • Use calipers to measure the width and length of the tab. • Compare the width to 35mm. • Compare the length to 18mm | if the width is less than 35mm and the length is greater than 18mm then the test is passed.

4.1. Tests
Test ID | Description | Testing Procedure | Pass/Fail Criteria
AT05 | Measure the width and length of the entire power board. | • Use calipers to measure the length of the entire power board. • Compare the length against 100mm. | If the length is less than 100mm then the test is passed, otherwise it is failed.
AT06 | Calculate the total com-ponent cost and verify on the JLCPCB website. | • Go to the online JLCPCB website and add all components to the cart. • Click on checkout and obtain a final sum for the component cost (ex-cluding the board fees but including the extended part fee). | If the price for one board is less than $ 8.25 then the test is passed.
AT07 | Check that the switch behaves correctly. | • Move the switch from ’OFF’ to ’ON’ position. • Using a multimeter, do a continu-ity test with one probe on TP3 and the other on TP4. | If the multimeter beeps when the switch is in the ’OFF’ posi-tion, the test is failed. If there is a beep when it moves to the ’ON’ position, the test is passed.
AT08 | Code the microcon-troller to display the state of charge from the ADC pin. | • Assume AT02 and AT07 have been passed. • Write code for the microcon-troller’s ADC pin to output the state of charge to an LCD Display or LEDs. | Verify the circuit works by reading the output of the LCD Display or monitoring the LED blinking.
AT09 | Check that the battery charging circuit is oper-ational. | • Use TP1 to verify that the input voltage is 5V as expected. • Use the LED indicators in the circuit to monitor the state of the battery. | If the red LED is on and the green is off: the battery is charging. If the red LED is off and the green LED is on: the battery has finished charg-ing. If it is plugged in and both LEDs are off then the in-put voltage is too low or the temperature of the battery is out of the acceptable range or there is no battery connected and the test failed

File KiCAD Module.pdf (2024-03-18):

Hello and Welcome
As we are slowly moving back to instructed learning (which I prefer) there are still time complications that prevent the contact time necessary to make it fully instructed. This is my running document over the years.

These documents cover all the material and more for what you would need to achieve 100% in the MEC1003F course provided you are careful. Designing hardware is very detail specific and a willingness to deep dive is vital. Please start by looking at the first link in the following sentence if you are a 1st year.

With the current context of COVID19, I have decided to link useful material here. (https://docs.google.com/document/d/1IGlWmJ9JWJ1rSiJNNF90vrDmYA_OmHIf84li2hzz8N4/edit)

Only proceed further if you choose to do so…

The following notes are made for anyone wishing to take their PCB design further, if you are part of the 1st year class, we will go through this material as we progress through the class, but I will keep these notes up if any of my other students stumble across the material or a 1st year is especially keen.

# Simplified KiCAD Module

It would be foolish to make notes/videos on KiCAD as there is the help functionality, a massive community and as new versions come out things might change slightly. V6 came out 2021 Dec 25th. So if you are stuck use F1 or Google.

However with that said there is always some underlying structure which helps with regard to good practises.

This starts out as a guide to making a simple PCB Project, but then as you need to delve deeper into the finer details - more information is linked in this document.

If you go through:
Downloading KiCAD
KiCAD Cheatsheet (https://drive.google.com/file/d/1EnAFGWXD5rdyPgKgoxY4G4jNVG_Y5jbQ/view?usp=sharing)
Project
Schematic
PCB
Gerbers
Assembly Files (Optional)
Designing for Manufacture

You should have a completed PCB - If your board was simple enough.

# Downloading KiCAD

KiCAD is a free service, it is cross platform and freely downloadable from here. (http://kicad-pcb.org/download/) It isnt that small, so unless you have decent internet at home. I suggest you do it on campus.

The first step would be understanding the file structure

## Project:

The project is effectively the container for all your documents, if you forget to add everything to a project, you cannot link your files to each other which is very NB… (When opening your work, open the project.)

1. File -> New -> Project.

In general I find if you click on the items from left to right you following the correct order.

## Schematic:

1. Whenever you come back to a project or show a project to anyone else, the first point is to look at the information in the bottom right. Board Name, Who made it, which revision are you showing me, how old is it? Board setup (2nd from left I think)
2. Save (Ctrl+S)
3. Place your components (A)
4. Join the components together with wires(W)Wire. Use Supply symbols and Ports where possible
5. Save (Ctrl+S)
6. Think about test points, modularity, mounting holes then add them (Not necessary for 1st years)
7. Save (Ctrl+S)
8. Annotate your schematic
9. Run an ERC (Often need to set the rules for it first)
10. Assign Footprints

## PCB:

This is where mechanical meets electrical, think connector placement, heating issues, ingress, good layout.

1. Setup -> Layer Setup
2. Design Rules
a. Width - There is no 1 size… Choose intelligently (applies to a,b,c)
b. Clearance Manufacturing Board Outline Clearance
c. Hole Size
d. Silkscreen

Some Intelligent numbers could be: (It really depends on PCB)
a. 0.25mm | 0.6mm | 2mm
b. 0.4mm (easy board - noob soldering) | 0.25mm (difficult board - skilled soldering)
c. 0.5mm
d. 0.6mm min
e. Not important
3. Save
4. Import from schematic
5. Move components around find suitable modularization
6. Wire Sections
a. Manual Routing / Active Routing / Guided Routing
7. Create Outline (Sometimes moved to point 5)
8. Legend/Silkscreen

## Gerbers:

In order to manufacture your boards, you need to submit Gerbers to the manufacturing plant. A Gerber file is associated for each process in the manufacturing step. This would typically be each layer in your stackup.

Top Silk
Top Stop/Mask
Top Cu
Edge Outline
Bottom Cu
Bottom Stop/Mask
Bottom Silk

Plated Through Hole (PTH)
No(n/t) Plated Through Hole (NPTH) Optional:
Top Paste and Bottom Paste

Notes regarding my KiCAD Lecture 3 (https://docs.google.com/document/d/1G7eEZA7zs2kmy6n-NMIijcfioM0nD_dVto_-XYZHiAI/edit?usp=sharing)

I made a file for historically manufacturing from a local supplier Trax.
Assistance to Use the TraX PCB manufacturing discount. (https://docs.google.com/document/d/1UpcKuZbNOQ72QixBxMgy-SHJSjzI6hitiBqPTH83V2w/edit?usp=sharing) - Legacy
Regrettably, the cost benefits and timeframes with TraX are no longer deemed optimal and most of my manufacturing is done in China.

To do it (without plugin):

In PCB view, File → Plot → Gerber files. In the layers tab select the layers you want.
OK (That will give you 7 files)

Then for the final file (NC Drill File)
In PCB view, File → Fabrication Outputs → Drill file. OK (That will give you 2 files)

X is your Filename.

Convert from | Convert to
KiCAD | Altium | Trax (Legacy)
X-F.Cu.gbr | X.gtl (Gerber Top Layer) | Top Layer.gtl
X-F.SilkS.gbr | X.gto (Gerber Top Overlay) | Top Legend.gto
X-F.Mask.gbr | X.gts (Gerber Top Stop) | Top Stop.gts
X-Edge.Cuts.gbr | X.gm1 (Mechanical 1 Layer) | Outline.gm1
X-PTH.drl | X.TXT (NC Drill file) | Drill.TXT
X-NPTH.drl | (No Non Plated Holes) | NPTH.drl
X-B.Cu.gbr | X.gbl (Gerber Bottom Layer) | Bottom Layer.gbl
X-B.SilkS.gbr | X.gbo (Gerber Bottom Overlay) | Bottom Legend.gbo
X-B.Mask.gbr | X.gbs (Gerber Bottom Stop) | Bottom Stop.gbs

X-F.Paste.gbr

X-B.Paste.gbr

# Assembly Files (Optional)

If you are taking files to an assembly plant. There are a few requirements you would need to submit.
BOM | (Schematic View)
PDF of Docs | (Anywhere)
Pick and Place Files | (PCB View)
Paste file(s) for Stencil | (PCB View)

## Useful Information I have learnt through my mistakes

- Whenever you make a mistake - it doesn't matter who’s fault it actually was - you look like the idiot. You are responsible for the projects you make and you need to check everything before having the opinion that everything will work.

## Designing for Manufacture

Simply connecting tracks to pins might produce a PCB that works, but there is vastly more that can be done to optimise the process. I am compiling a document to highlight some of the lessons I have learnt over the years with regard to designing for manufacture.

Help in designing for manufacture (https://docs.google.com/document/d/1S9V9-ZjE7nPpIeefd86OcMlLAtxHmJ97o1IgDoaCQ6c/edit?usp=sharing)

http://www.ti.com/lit/ds/symlink/lm556.pdf

http://www.seoulsemicon.com/upload2/STW8T16C.pdfhttp://www.ttelectronics.com/sites/default/files/download-files/Datasheet_PanelPot_P090 Series.pdf (http://www.ttelectronics.com/sites/default/files/download-files/Datasheet_PanelPot_P090Series.pdf)

# 2019 Session 4 - Kept here for reference

Lecture 4 - Application

This year, I thought starting the process for building a power supply would be useful. The first 6 circuits are solutions to the problem of how to make it work, however none of these circuits have the ability to survive when a mistake happens.

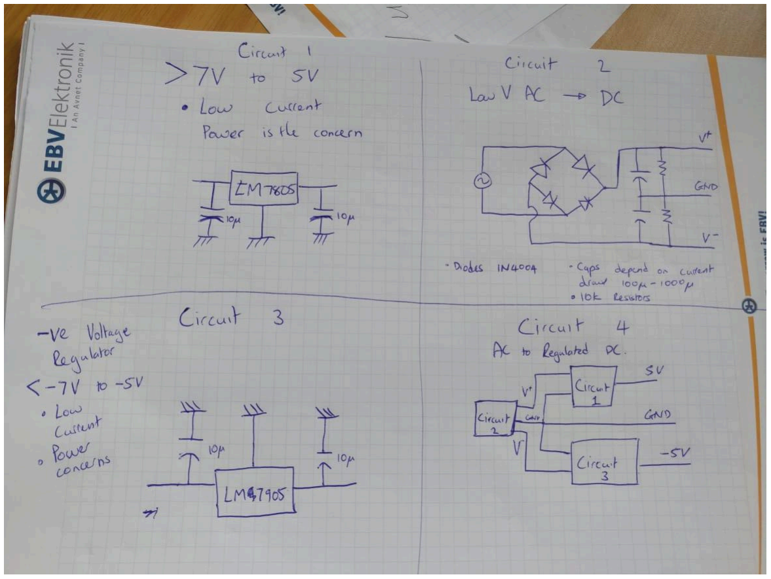
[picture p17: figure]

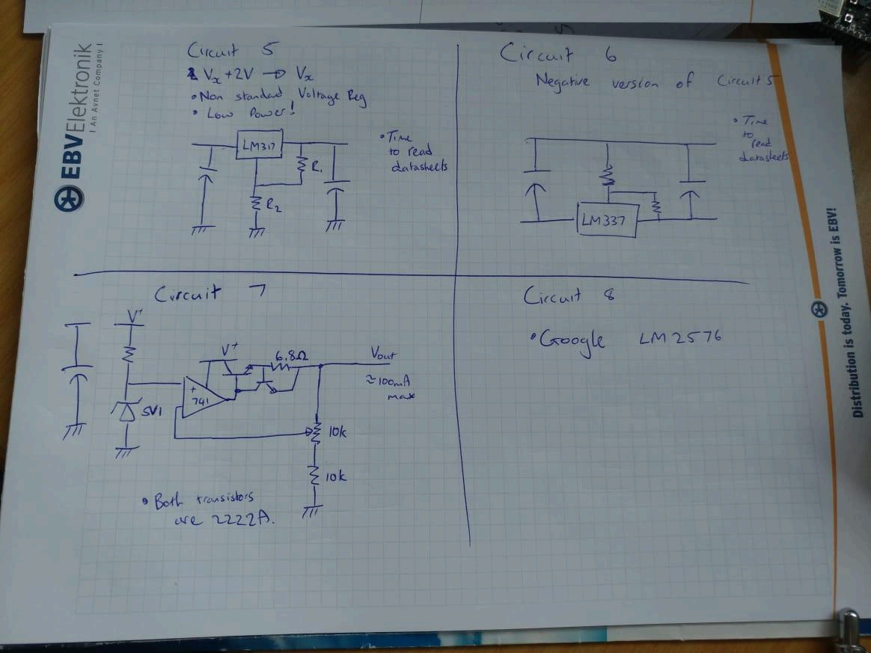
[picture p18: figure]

Then you could use the following components by still providing the necessary from Circuit 2.

OR

you could take apart a Computer PSU if you have one lying around. I have a how to on my Useful linker and then use the below links for further control.

Purchasable Buck 1 (https://www.netram.co.za/3384-5a-cccv-buck-step-down-power-module-xl4015.html)
Purchasable Buck 2 (https://shop.communica.co.za/products/acm-dc-dc-buck-module-0-8-20v-2a)

Okay again these are the basics… I would STRONGLY recommend:

- fuses to ensure if/when something goes wrong the fuse blows and you don't start a fire.
- Power LEDs to confirm your voltages are working

Voltage Monitoring (http://www.communica.co.za/Catalog/Details/P3238432112) - Local
Voltage Monitoring (https://www.banggood.com/Geekcreit-0_28-Inch-2_5V-30V-Mini-Digital-Volt-Meter-Voltage-Tester-Voltmeter-p-974258.html?ID=228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) - China

Could add the following device to get a readout for your voltage. Then we could also measure the current using an INA169 and measure the output voltage with the above voltage monitoring which would then be displaying the current.

Okay, I think that is enough to cover all the students in the class. Goodluck.

https://www.youtube.com/watch?v=5Be7XOMmPQE

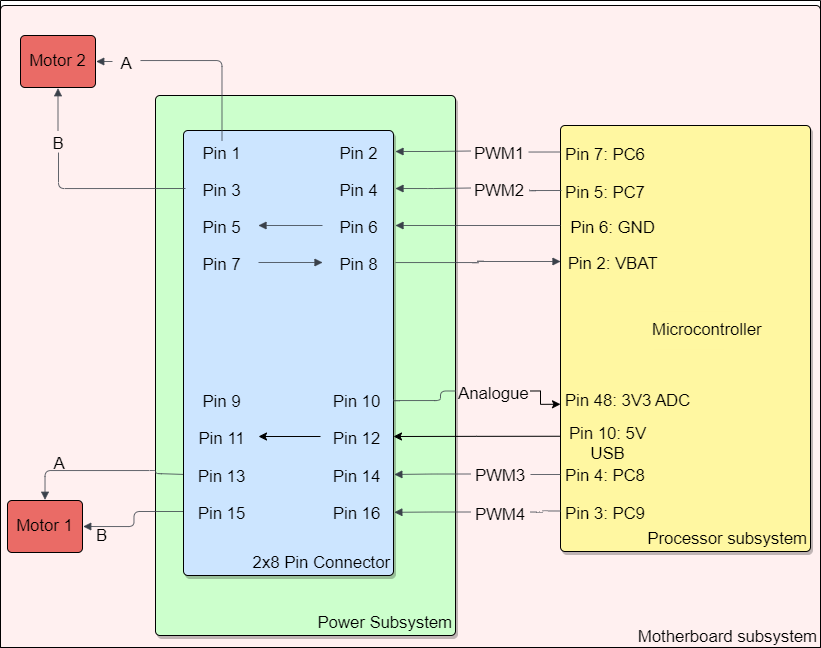
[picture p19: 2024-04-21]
Power Subsystem/Interim Report Figures/interface (1).png

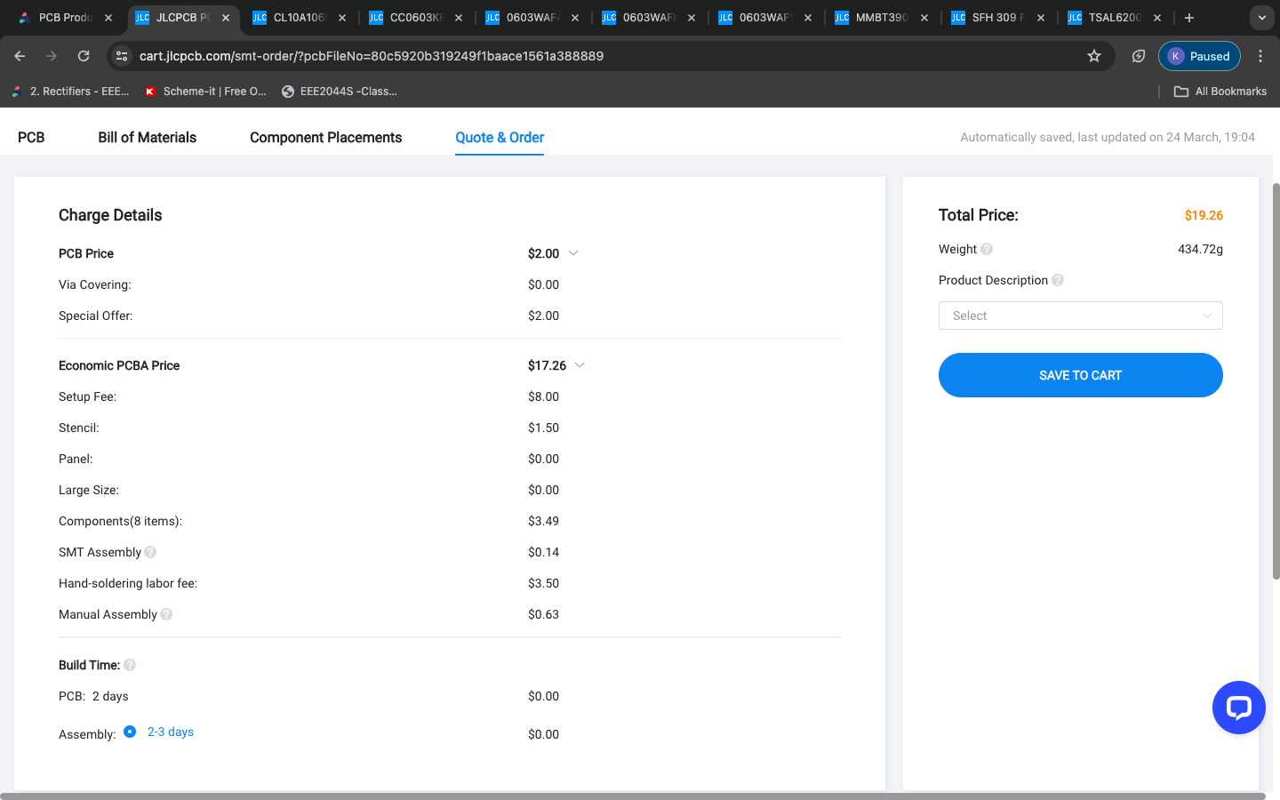
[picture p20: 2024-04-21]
Sensing Subsystem/PCB Design/PLLKAS005_EEE3088F/jlcpcb/production_files/EEE3088F_Project_JLCPCBacceptance_PLLKAS005.png

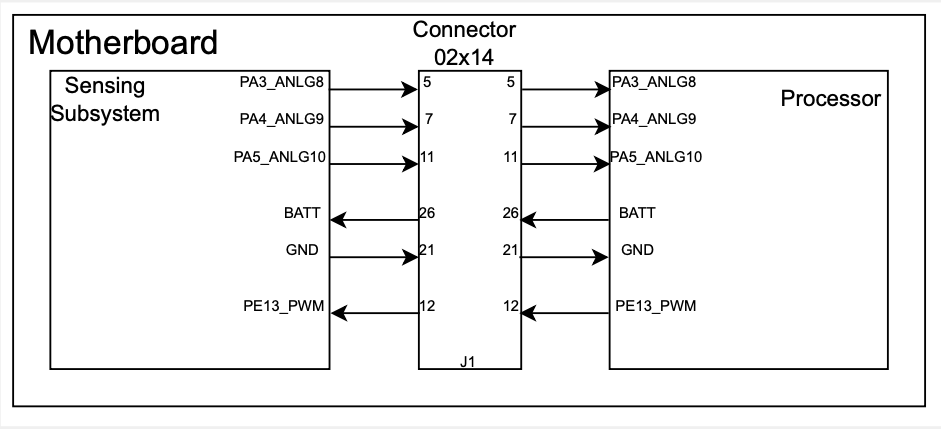
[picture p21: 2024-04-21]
Sensing Subsystem/Interim Report/interfacing_diag.png

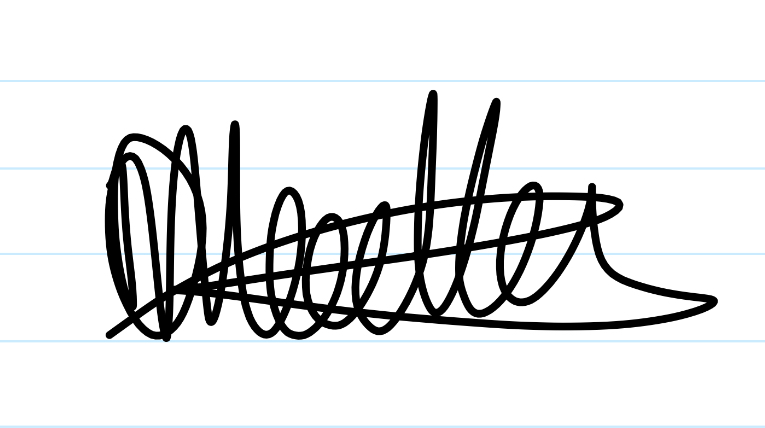
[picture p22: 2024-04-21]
Power Subsystem/Interim Report Figures/signature (2).jpg

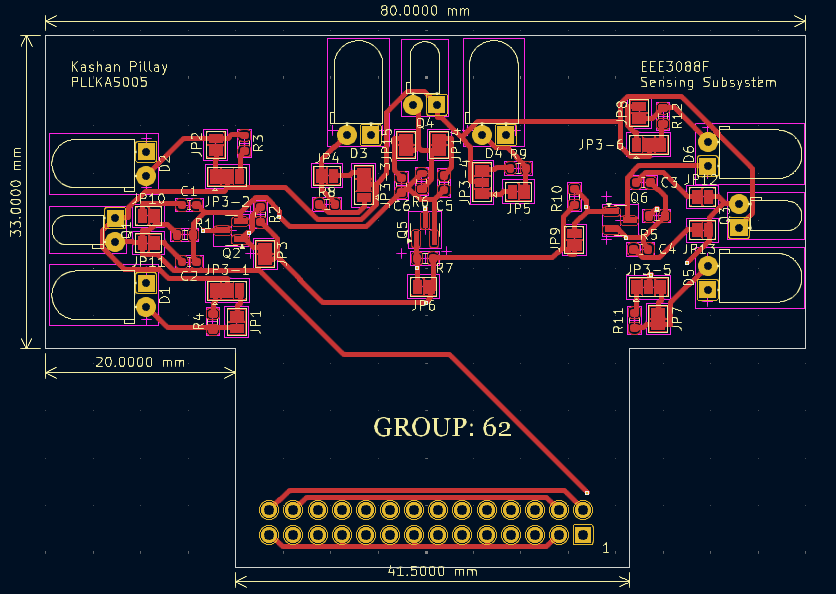
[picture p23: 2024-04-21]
Sensing Subsystem/Interim Report/pcb_Front.png

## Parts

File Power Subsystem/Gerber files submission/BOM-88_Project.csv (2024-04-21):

Comment | Designator | Footprint | LCSC
TP4056-42-ESOP8 | U1 | TP4056-42-ESOP8_TPW | C16581
10uF | C1,C2,C5 | C_0603_1608Metric | C19702
1k | R1,R2,R6,R7 | R_0603_1608Metric | C21190
19-217/BHC-ZL1M2RY/3T | LED1 | LED_19-217&slash_BHC-ZL1M2RY&slash_3T_EVE-M | C2286
1 | R3,R5,R8,R9 | R_1206_3216Metric | C22936
2k | R10 | R_0603_1608Metric | C22975
4k | R11 | R_0603_1608Metric | C23018
2.2uF | C3 | C_0603_1608Metric | C23630
19-217/BHC-ZL1M2RY/3T | LED2 | LED_19-217&slash_BHC-ZL1M2RY&slash_3T_EVE-M | C2986059
3k | R4 | R_0603_1608Metric | C4211
DRV8833PWPR | U2 | HTSSOP-16-1EP_4.4x5mm_P0.65mm_EP3.4x5mm | C50506
10nF | C4 | C_0603_1608Metric | C57112
SS-12D10G5 | SW1 | SS-12D10G5_XKB | C7431054

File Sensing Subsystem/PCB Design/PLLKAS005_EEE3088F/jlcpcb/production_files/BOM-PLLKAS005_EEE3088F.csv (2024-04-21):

Comment | Designator | Footprint | LCSC
100nF | C2,C4,C6 | C_0603_1608Metric | C14663
10uF | C1,C3,C5 | C_0603_1608Metric | C19702
MMBT3904 | Q2,Q5,Q6 | SOT-23 | C20526
42 | R11,R12,R3,R4,R8,R9 | R_0603_1608Metric | C23182
780 | R10,R2,R7 | R_0603_1608Metric | C23253
10k | R1,R5,R6 | R_0603_1608Metric | C25804
SFH309 | Q1,Q3,Q4 | LED_D3.0mm_Horizontal_O1.27mm_Z2.0mm_Clear | C2900253
LED | D1,D2,D3,D4,D5,D6 | LED_D5.0mm_Horizontal_O1.27mm_Z3.0mm_IRBlack | C55528

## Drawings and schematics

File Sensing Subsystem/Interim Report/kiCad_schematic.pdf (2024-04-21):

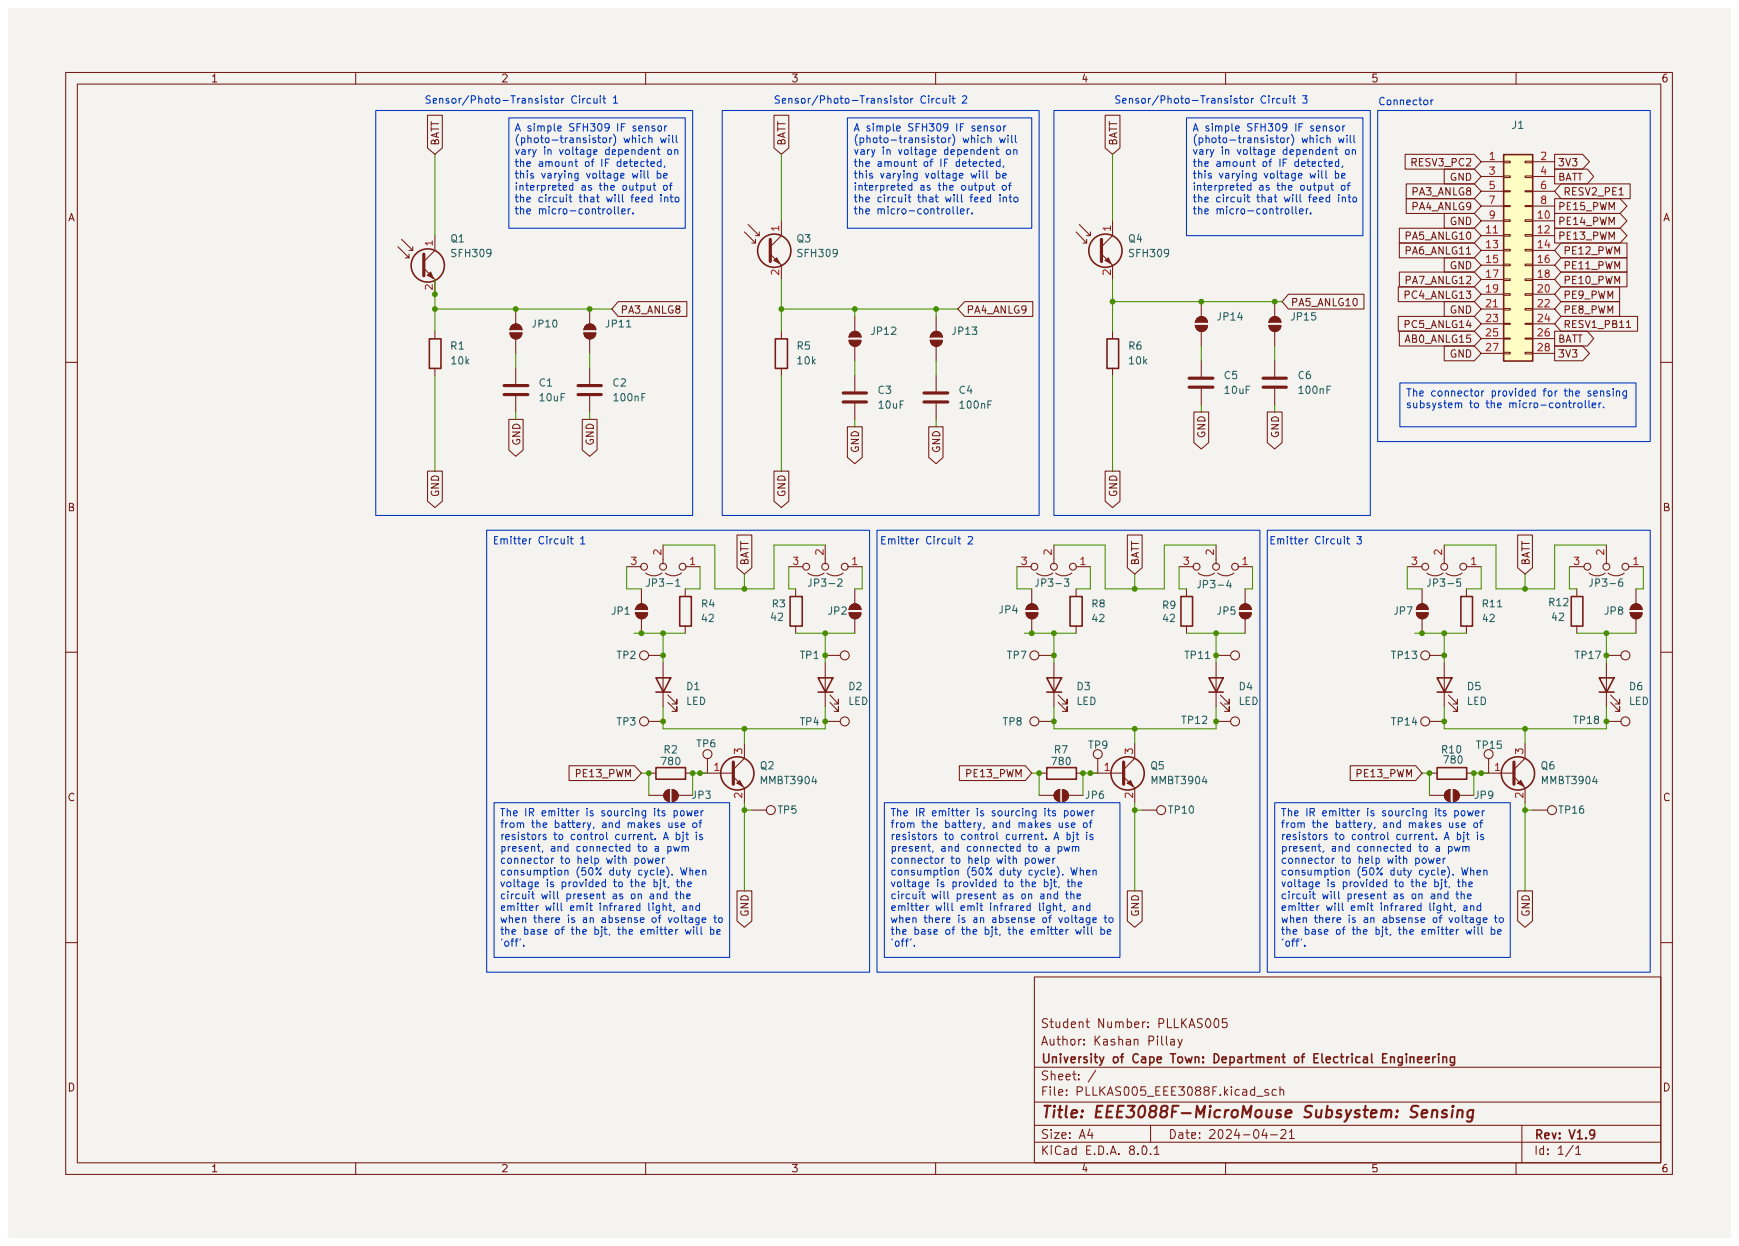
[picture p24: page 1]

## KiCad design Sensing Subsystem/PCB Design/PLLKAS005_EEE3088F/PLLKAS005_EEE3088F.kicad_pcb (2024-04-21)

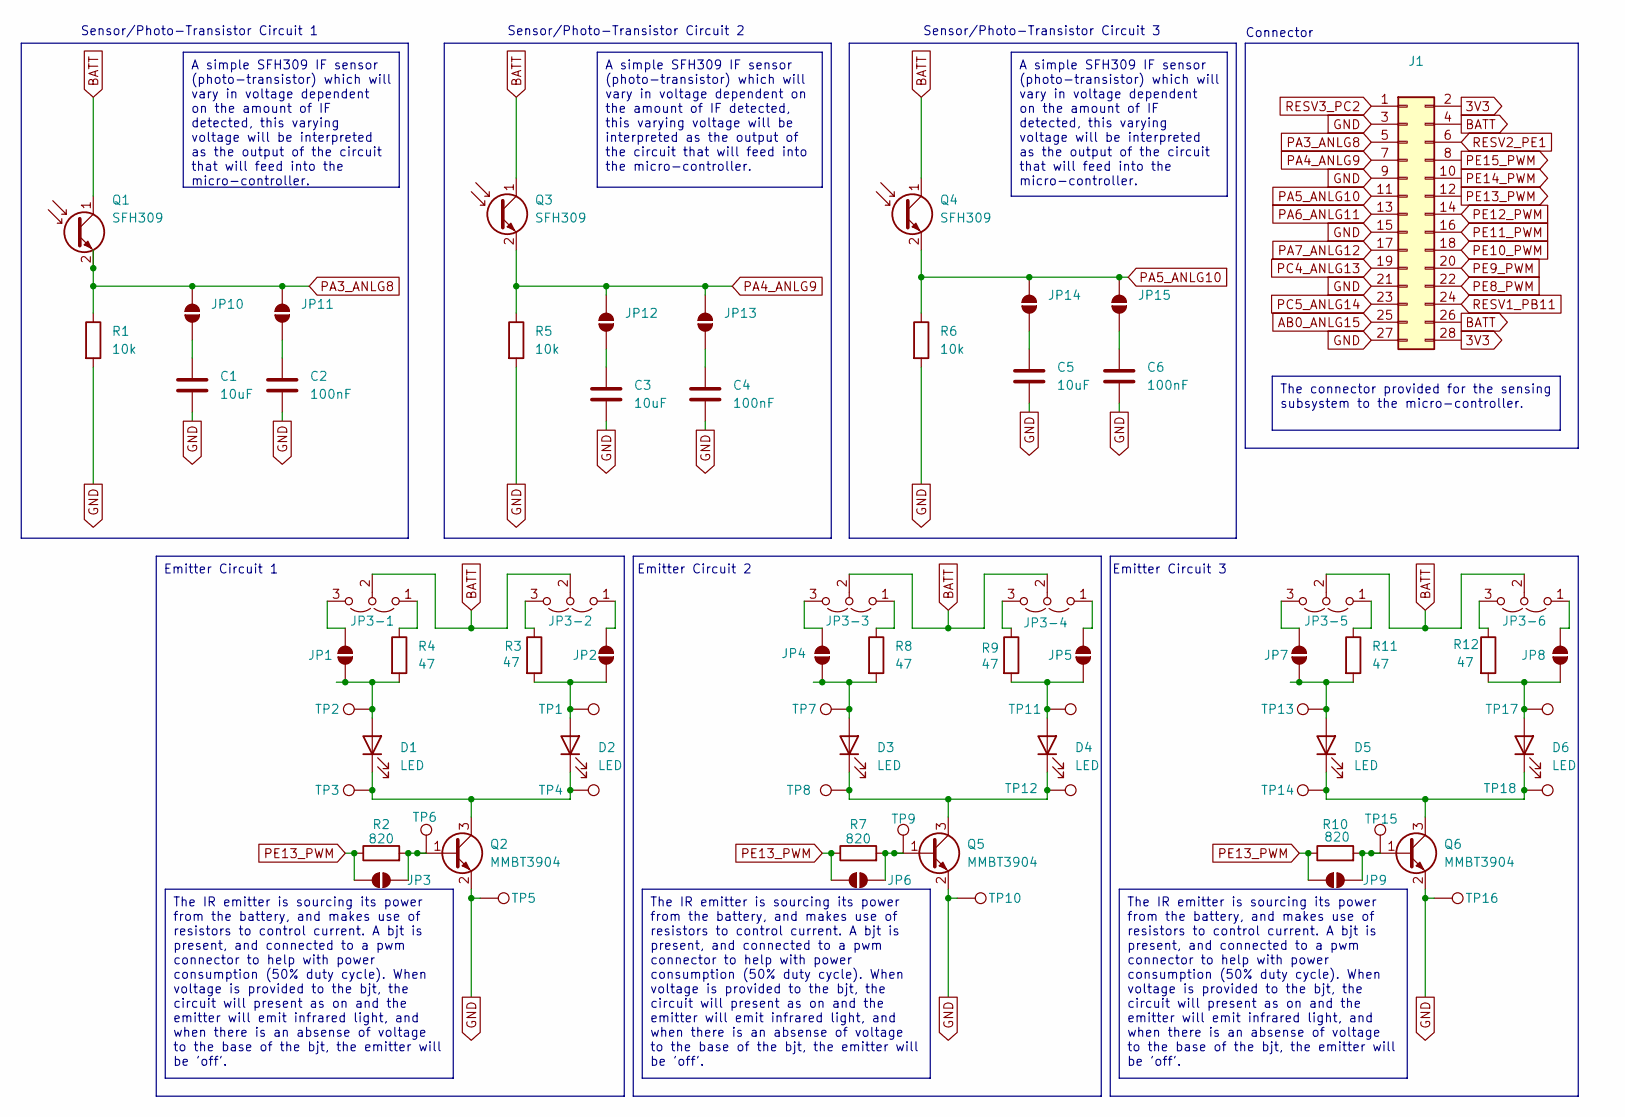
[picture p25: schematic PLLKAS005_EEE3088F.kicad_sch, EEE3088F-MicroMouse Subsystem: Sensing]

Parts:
C1, C3, C5: 10uF; C_0603_1608Metric
C2, C4, C6: 100nF; C_0603_1608Metric
D1, D2, D3, D4, D5, D6: LED; LED_D5.0mm_Horizontal_O1.27mm_Z3.0mm_IRBlack
J1: Conn_02x14_Odd_Even; PinHeader_2x14_P2.54mm_Vertical
JP1, JP2, JP3, JP4, JP5, JP6, JP7, JP8, JP9, JP10, JP11, JP12, JP13, JP14, JP15: SolderJumper_2_Open; SolderJumper-2_P1.3mm_Open_Pad1.0x1.5mm
JP3-1, JP3-2, JP3-3, JP3-4, JP3-5, JP3-6: Jumper_3_Open; SolderJumper-3_P1.3mm_Open_Pad1.0x1.5mm
Q1, Q3, Q4: SFH309; LED_D3.0mm_Horizontal_O1.27mm_Z2.0mm_Clear
Q2, Q5, Q6: MMBT3904; SOT-23
R1, R5, R6: 10k; R_0603_1608Metric
R2, R7, R10: 820; R_0603_1608Metric
R3, R4, R8, R9, R11, R12: 47; R_0603_1608Metric
TP1, TP2, TP3, TP4, TP5, TP6, TP7, TP8, TP9, TP10, TP11, TP12, TP13, TP14, TP15, TP16, TP17, TP18: TestPoint; TestPoint_Pad_D3.0mm

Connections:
3V3: J1.2, J1.28
AB0: J1.25
BATT: J1.4, J1.26, JP3-1.2 (C), JP3-2.2 (C), JP3-3.2 (C), JP3-4.2 (C), JP3-5.2 (C), JP3-6.2 (C), Q1.1 (C), Q3.1 (C), Q4.1 (C)
GND: C1.2, C2.2, C3.2, C4.2, C5.2, C6.2, J1.3, J1.9, J1.15, J1.21, J1.27, Q2.2 (E), Q5.2 (E), Q6.2 (E), R1.2, R5.2, R6.2, TP5.1, TP10.1, TP16.1
unnamed: D1.2 (A), JP1.1 (A), R4.2, TP2.1
unnamed: D1.1 (K), D2.1 (K), Q2.3 (C), TP3.1, TP4.1
unnamed: D2.2 (A), JP2.1 (A), R3.2, TP1.1
unnamed: D3.2 (A), JP4.1 (A), R8.2, TP7.1
unnamed: D3.1 (K), D4.1 (K), Q5.3 (C), TP8.1, TP12.1
unnamed: D4.2 (A), JP5.1 (A), R9.2, TP11.1
unnamed: D5.2 (A), JP7.1 (A), R11.2, TP13.1
unnamed: D5.1 (K), D6.1 (K), Q6.3 (C), TP14.1, TP18.1
unnamed: D6.2 (A), JP8.1 (A), R12.2, TP17.1
unnamed: JP1.2 (B), JP3-1.3 (B)
unnamed: JP2.2 (B), JP3-2.1 (A)
unnamed: JP3-1.1 (A), R4.1
unnamed: JP3-2.3 (B), R3.1
unnamed: JP3-3.1 (A), R8.1
unnamed: JP3-3.3 (B), JP4.2 (B)
unnamed: JP3-4.1 (A), JP5.2 (B)
unnamed: JP3-4.3 (B), R9.1
unnamed: JP3-5.1 (A), R11.1
unnamed: JP3-5.3 (B), JP7.2 (B)
unnamed: JP3-6.1 (A), JP8.2 (B)
unnamed: JP3-6.3 (B), R12.1
unnamed: JP3.1 (A), Q2.1 (B), R2.2, TP6.1
unnamed: JP6.1 (A), Q5.1 (B), R7.2, TP9.1
unnamed: JP9.1 (A), Q6.1 (B), R10.2, TP15.1
unnamed: C1.1, JP10.1 (A)
unnamed: C2.1, JP11.1 (A)
unnamed: C3.1, JP12.1 (A)
unnamed: C4.1, JP13.1 (A)
unnamed: C5.1, JP14.1 (A)
unnamed: C6.1, JP15.1 (A)
PA3: J1.5, JP10.2 (B), JP11.2 (B), Q1.2 (E), R1.1
PA4: J1.7, JP12.2 (B), JP13.2 (B), Q3.2 (E), R5.1
PA5: J1.11, JP14.2 (B), JP15.2 (B), Q4.2 (E), R6.1
PA6: J1.13
PA7: J1.17
PC4: J1.19
PC5: J1.23
PE8: J1.22
PE9: J1.20
PE10: J1.18
PE11: J1.16
PE12: J1.14
PE13: J1.12, JP3.2 (B), JP6.2 (B), JP9.2 (B), R2.1, R7.1, R10.1
PE14: J1.10
PE15: J1.8
RESV1: J1.24
RESV2: J1.6
RESV3: J1.1

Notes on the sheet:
The IR emitter is sourcing its power from the battery, and makes use of resistors to control current. A bjt is present, and connected to a pwm connector to help with power consumption (50% duty cycle). When voltage is provided to the bjt, the circuit will present as on and the emitter will emit inf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
A simple SFH309 IF sensor (photo-transistor) which will vary in voltage dependent on the amount of IF detected, this varying voltage will be interpreted as the output of the circuit that will feed into the micro-controller.
The connector provided for the sensing subsystem to the micro-controller.
Sensor/Photo-Transistor Circuit 2
Emitter Circuit 3
Sensor/Photo-Transistor Circuit 1
Sensor/Photo-Transistor Circuit 3
Connector
Emitter Circuit 1
Emitter Circuit 2

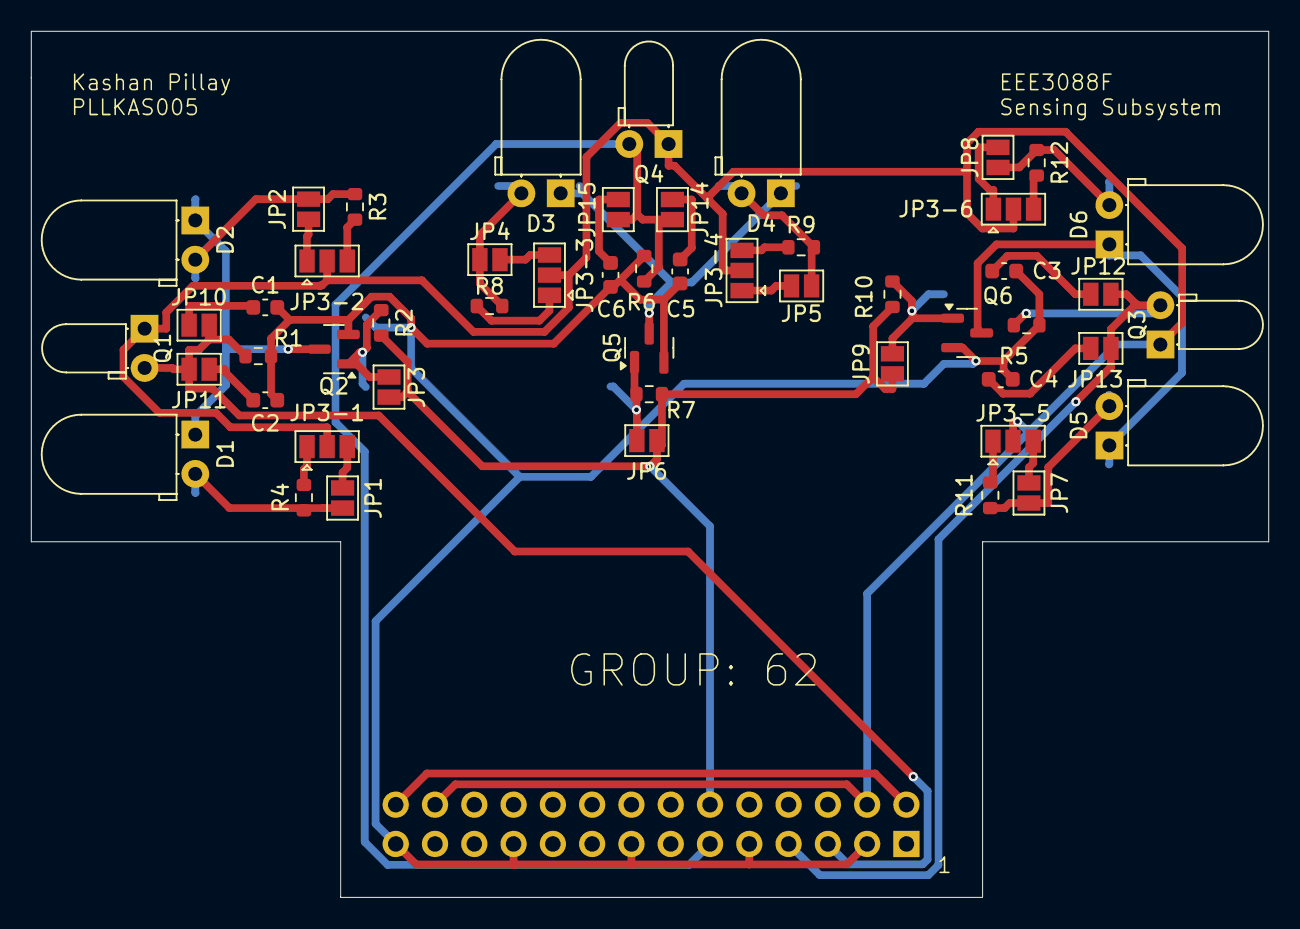
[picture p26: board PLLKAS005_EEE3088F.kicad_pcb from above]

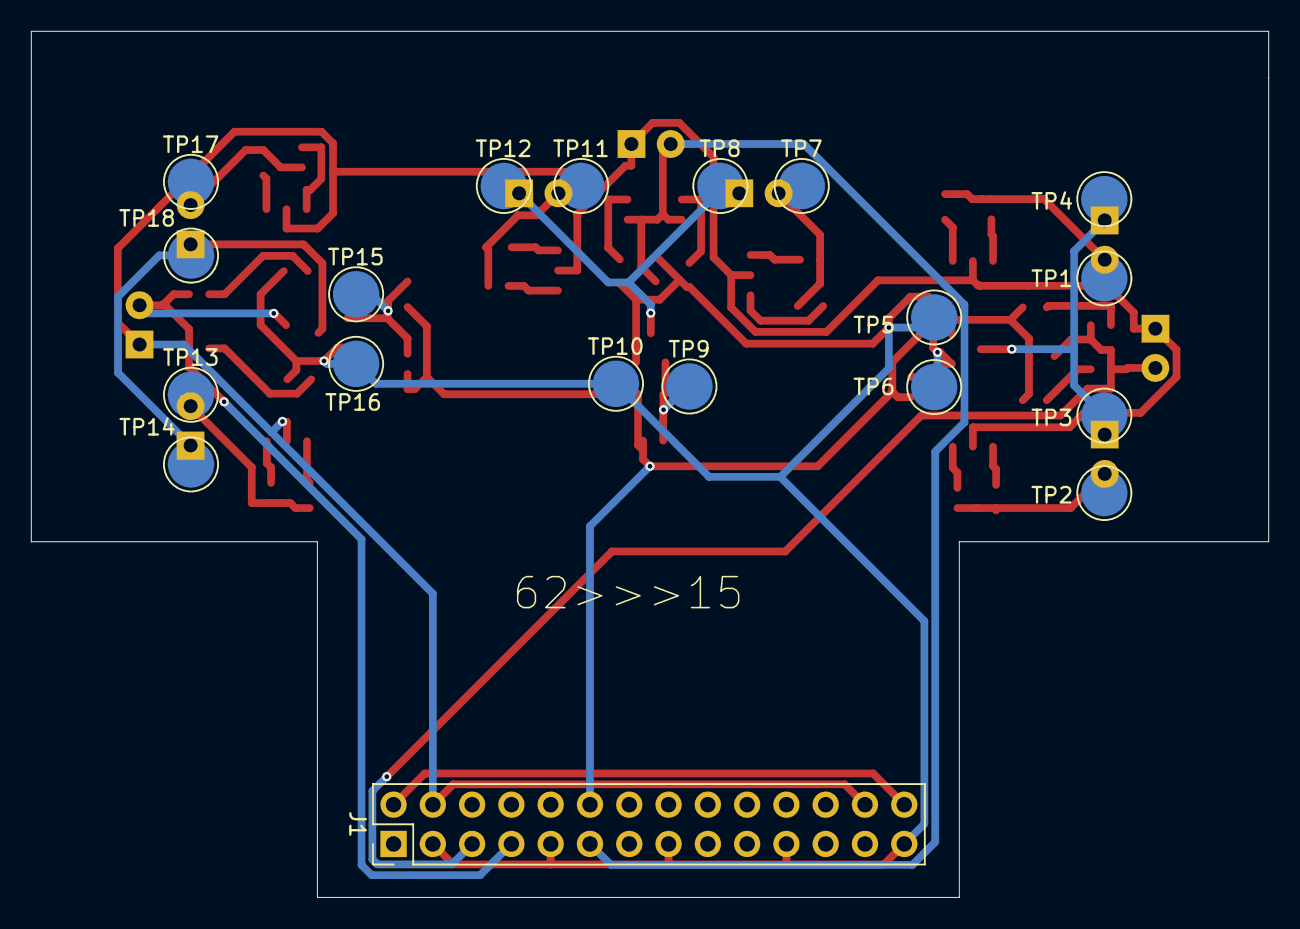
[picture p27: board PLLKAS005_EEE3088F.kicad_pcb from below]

Board: 2 copper layers, 80.0 x 56.0 mm, 70 parts (19 on the bottom side), 37 nets.

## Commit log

2024-03-18 Basic KiCAD assistance page.
2024-03-20 Motor Driver IC: Possible datasheet
    $0.894 and over 2000 stock
    Needs 5 capacitors and 3 resistors (estimate)
2024-03-22 IC for charging circuit
2024-03-22 RESISTOR: 10K datasheet
2024-04-21 Gerber file submission
    [88_Project-CuBottom.gbr, 88_Project-CuTop.gbr, 88_Project-EdgeCuts.gbr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]
2024-04-21 Addition of KiCad PCB Files and Interim Report Files
    [BOM-PLLKAS005_EEE3088F.csv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]
2024-04-21 The power subsystem information
    [88_Project-CuBottom.gbr, 88_Project-CuTop.gbr, 88_Project-EdgeCuts.gbr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]
